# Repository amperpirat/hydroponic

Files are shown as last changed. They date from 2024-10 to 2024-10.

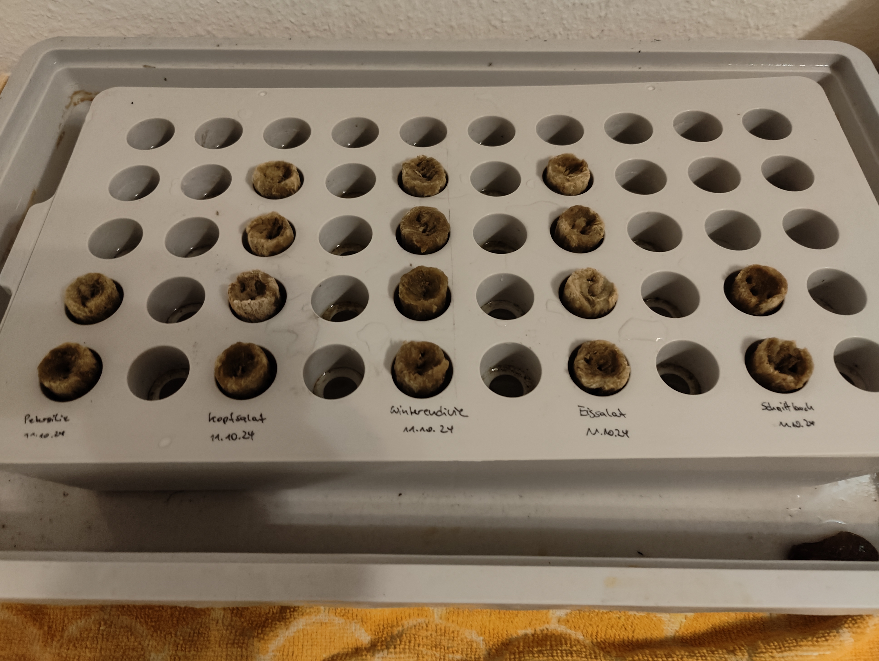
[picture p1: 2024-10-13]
Pictures/IMG20241011105112.jpg

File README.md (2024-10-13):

# hydroponic
indoor hydroponic system to grow herbs and salad

# Hardware
* ESP32 based PCB including DC/DC converter (5-60V input) and 2 relais
* 12V self-priming waterpumps (1-2l/min)
* GPIO 16 is wired to the emptying pump
* GPIO 17 is wired to the filling pump

# Software
* The hydroponic control is based on the home automation software espEASY (https://github.com/letscontrolit/ESPEasy/releases). Detailled documentation is available here: https://espeasy.readthedocs.io/en/latest/
* The control itself is based on rules (can be found as three files in the repo)
* configuration of devices is mandatory to be exactly the same
* MQTT for changing the timings, enable and disable the timer as well as monitoring the device
* configuration pictures can be found under pictures

# different status of the device
* 0	disabled
* 1	filling
* 2	holding
* 3	EMPTYING
* 4	waiting
* 5	inititial emptying
* 6	disable emptying
* 7	init
* 8	init done

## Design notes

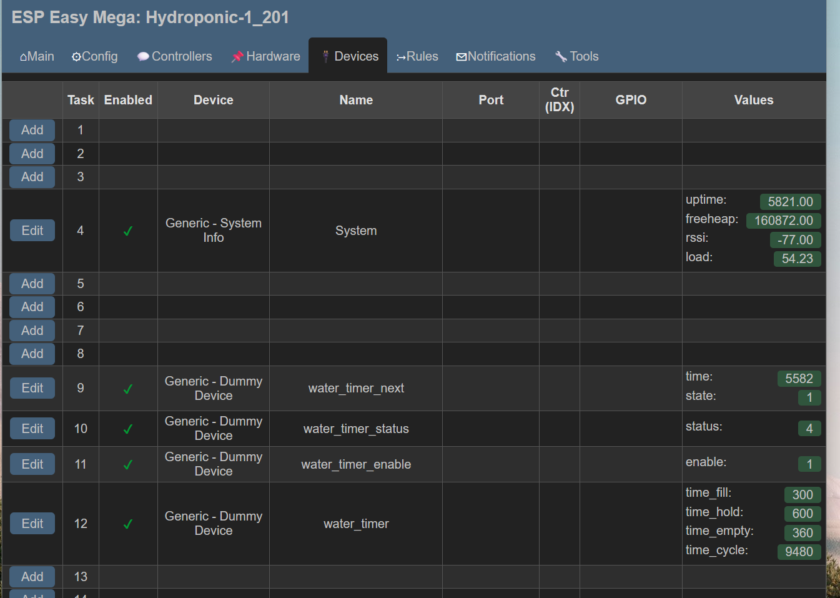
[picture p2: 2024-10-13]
Pictures/ESPEasy - config - devices.png

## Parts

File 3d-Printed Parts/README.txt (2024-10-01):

Print Settings

- 0.2mm with 0.4mm nozzle
- 15% infill
- support

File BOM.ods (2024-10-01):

 |  |  |  | 132,04 €
# | Name | Quantity | Price | Total Price | Source | Remarks
1 | Control Board; ESP32 | 2 | 13,99 € | 27,98 € | https://www.amazon.de/gp/product/B0CYSMFB49
2 | Waterpump | 2 | 9,59 € | 19,18 € | https://www.amazon.de/gp/product/B097PGDZTD
3 | Hose Connectors | 1 | 6,29 € | 6,29 € | https://www.amazon.de/dp/B0B5GB4KLH
4 | Spacer for Hoses | 1 |  | 0,00 € | Hydroponic spacer.step | 3D printed
5 | Lids | 12 |  | 0,00 € | Hydroponic lid.step | 3D printed; for unused plant containers
6 | Hydroponic Adapter | 1 |  | 0,00 € | Hydroponic adapter.step | 3D printed
7 | Hydroponic Set | 1 | 39,95 € | 39,95 € | https://www.amazon.de/gp/product/B07YB2NB7P
8 | Watercanister, 20l | 1 | 12,10 € | 12,10 € | https://www.amazon.de/gp/product/B01IGF7MY2
9 | Silicon hose | 3 | 4,39 € | 13,17 € | https://www.amazon.de/gp/product/B09R8X417G
10 | Cable Tie | 6 | 0,10 € | 0,60 €
11 | Screw M3*30 | 2 |  | 0,00 €
12 | Ruthex Gewindeeinsatz, M3 | 2 | 0,09 € | 0,18 € | https://www.amazon.de/gp/product/B08BCRZZS3
13 | Temp Sensor, DS18B20 | 1 | 3,60 € | 3,60 € | https://www.amazon.de/AZDelivery-digitaler-Temperatursensor-Temperaturf%C3%BChler-wasserdicht/dp/B07KNQJ3D7
14 | Power Supply, 12V 2A | 1 | 8,99 € | 8,99 € | https://www.amazon.de/Netzteil-Elektroauto-Externe-Festplatte-Keyboard-Schwarz/dp/B0CX5CBVN1
15 | Case for Control and Pump; bottom | 1 |  |  | Hydroponic watertank bottom.step
16 | Case for Control and Pump; top | 1

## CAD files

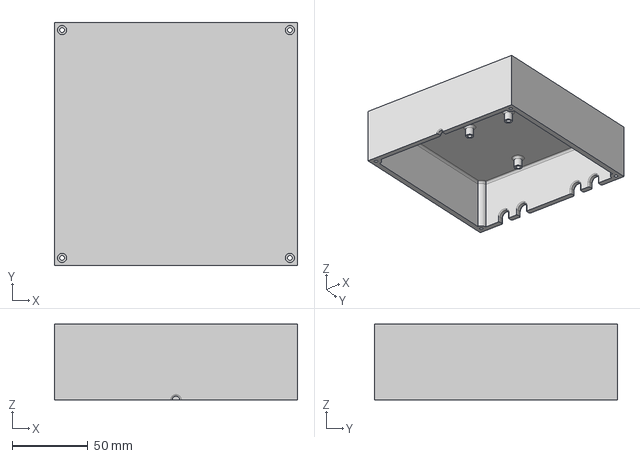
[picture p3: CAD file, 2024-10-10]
3d-Printed Parts/Hydroponic Watertank Top.step
160.0 x 160.0 x 50.0 mm

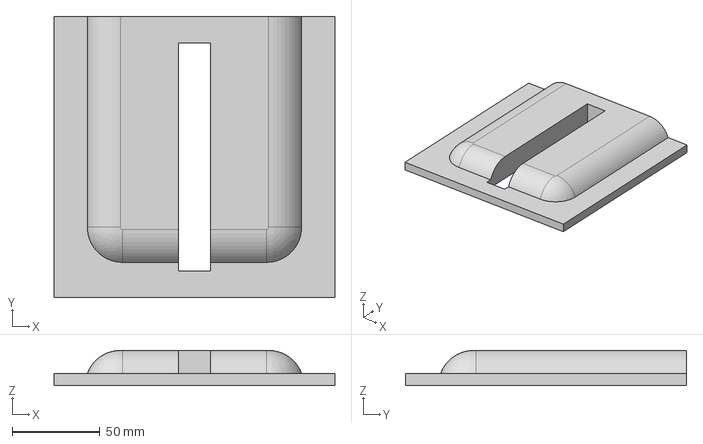
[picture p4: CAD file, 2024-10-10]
3d-Printed Parts/Hydroponic watertank bottom.step
160.0 x 160.0 x 20.0 mm

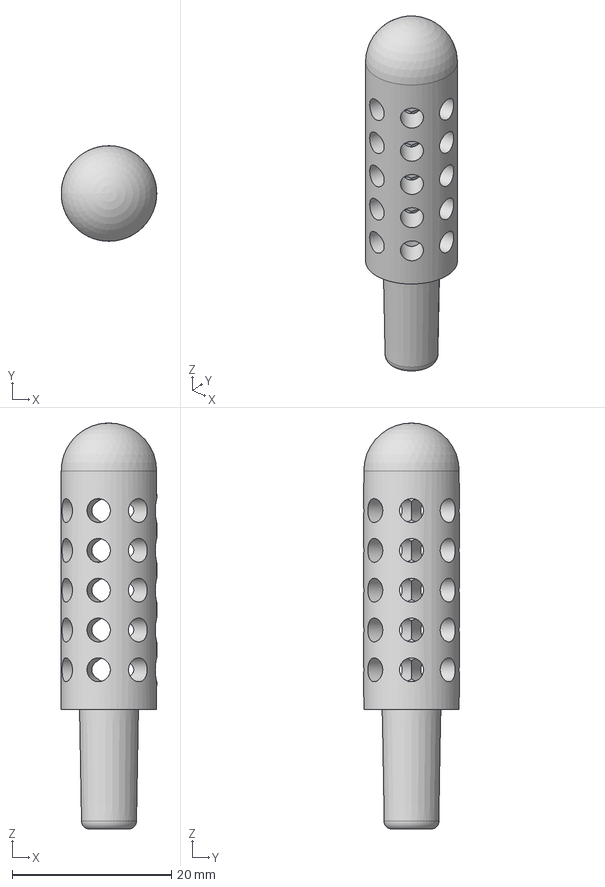
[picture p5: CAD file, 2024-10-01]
3d-Printed Parts/Hydroponic filter.step
12.0 x 12.0 x 51.0 mm

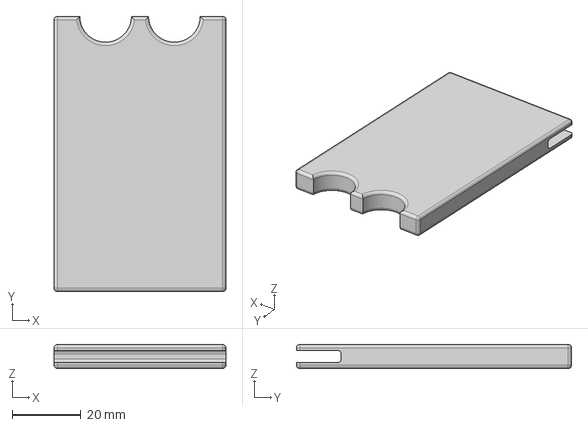
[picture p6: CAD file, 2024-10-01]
3d-Printed Parts/Hydroponic spacer.step
50.0 x 80.0 x 7.00 mm

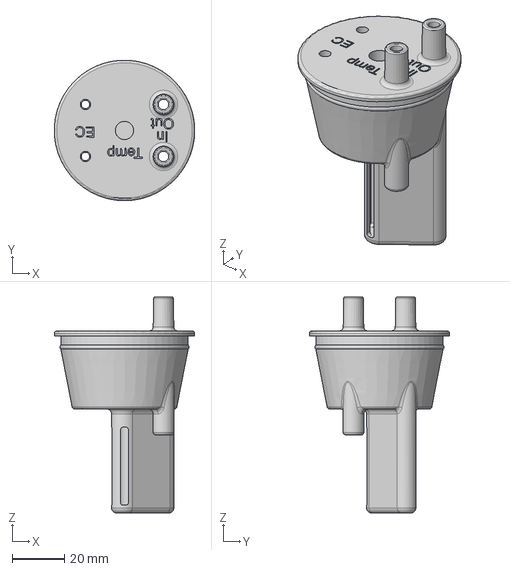
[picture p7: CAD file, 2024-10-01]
3d-Printed Parts/Hydroponic adapter.step
54.0 x 54.0 x 83.0 mm

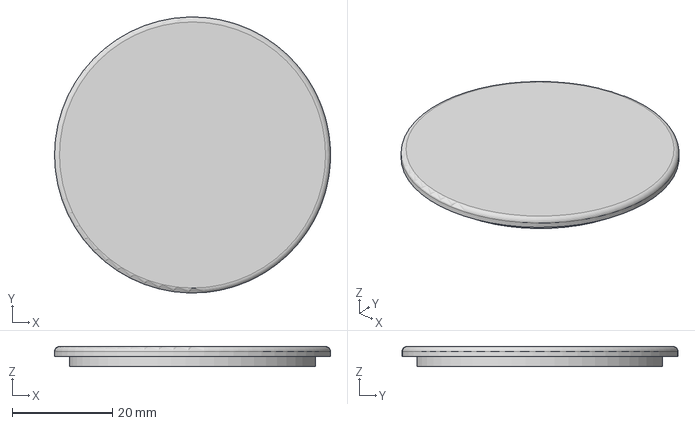
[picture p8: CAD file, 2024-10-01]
3d-Printed Parts/Hydroponic lid.step
55.0 x 55.0 x 4.00 mm

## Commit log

2024-10-01 add basic 3D printed parts to repo
    [Hydroponic adapter.step, Hydroponic lid.step, Hydroponic spacer v1.step]
2024-10-01 added print settings
2024-10-01 added 3d printed parts - part II
    [Hydroponic filter.step, Hydroponic watertank bottom.step]
2024-10-01 added BOM
    [BOM.ods, Hydroponic spacer.step]
2024-10-10 updated some 3D printed parts to the recent ESP32 PCB
    [Hydroponic Watertank Top.step, Hydroponic watertank bottom.step]
2024-10-10 add ESPeasy Ruleset for hydroponic timer and MQTT data control
